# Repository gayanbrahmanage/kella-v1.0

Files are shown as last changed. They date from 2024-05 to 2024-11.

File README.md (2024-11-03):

# kella-v1.0
 Humonoid Robot Development Project

 ### Base Design and Development
 <div style="display: flex;">
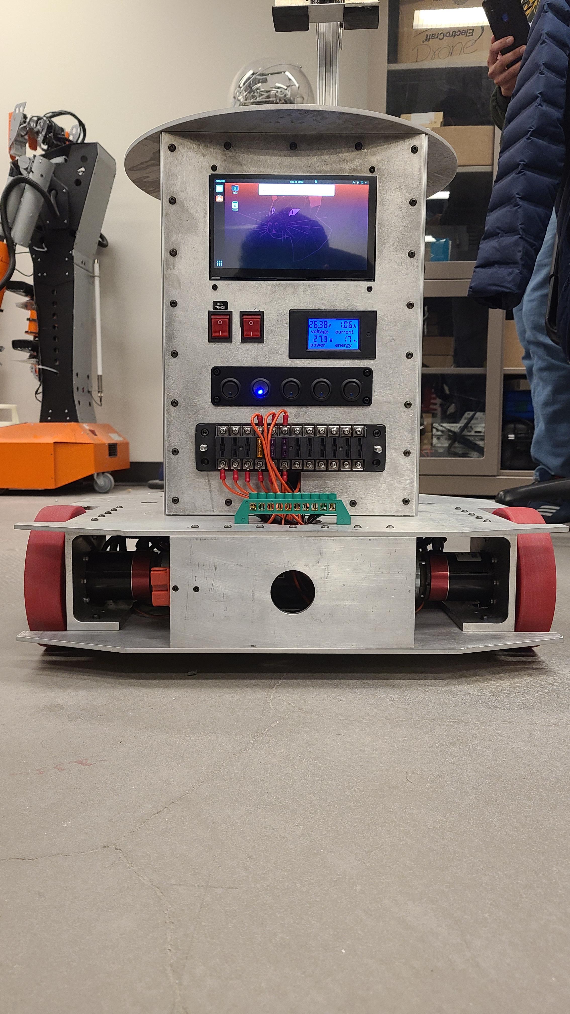
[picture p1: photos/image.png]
Example Image
 
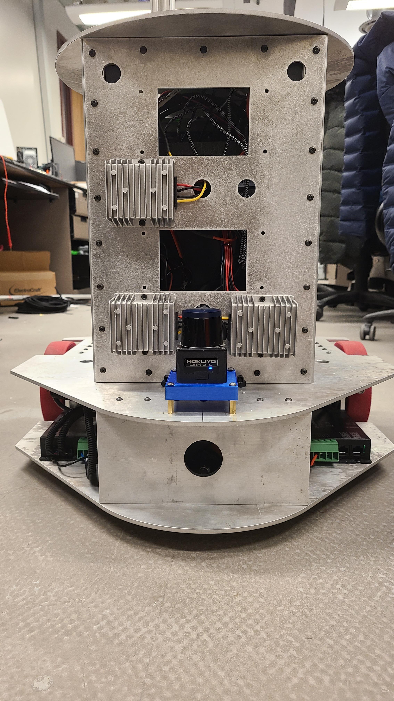
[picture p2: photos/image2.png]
Example Image
 
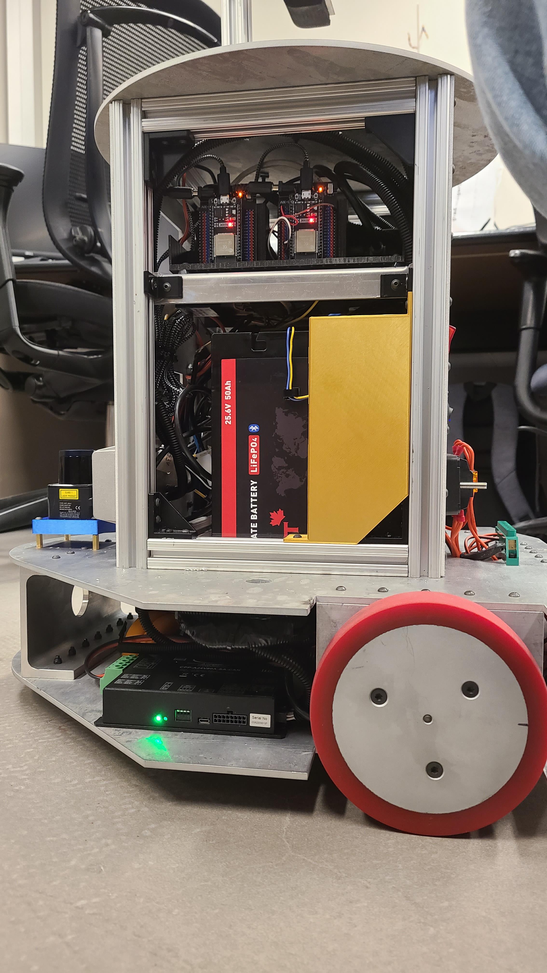
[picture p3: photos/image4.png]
Example Image
 
 </div>
 
 ### YouTube Video-Base Manual Mode Testing

My YouTube Video (https://www.youtube.com/watch?v=laG0K3bYE8s)

[Watch on YouTube](https://www.youtube.com/watch?v=laG0K3bYE8s)

My YouTube Video (https://www.youtube.com/watch?v=bEIRYtwlFlk)

# Design Power Point 

[View Design PPT](photos/pdf.pdf)

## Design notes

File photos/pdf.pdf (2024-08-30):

# Receptionist Robot

### Design and Development of A Humanoid Robot

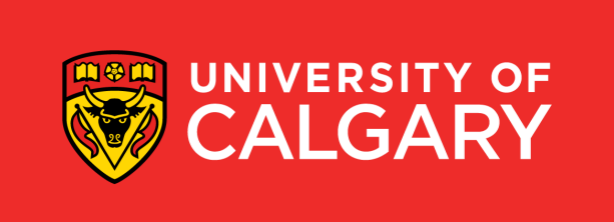
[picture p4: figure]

### 25 January 2022

2

# Modules (Electrical/Electronics)

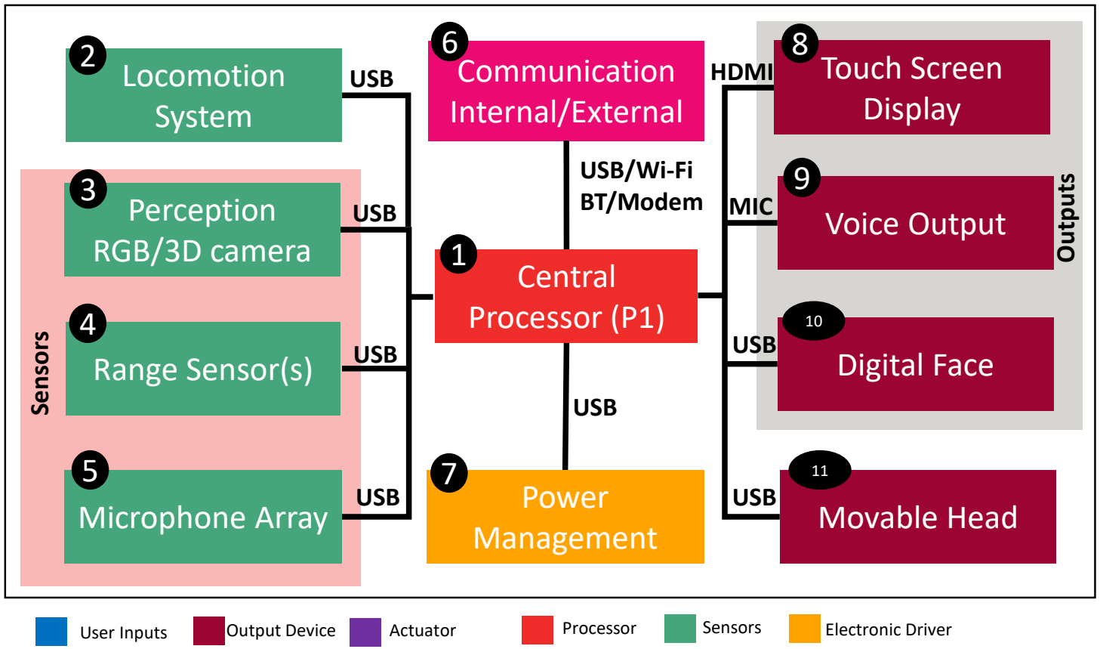
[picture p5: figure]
Locomotion System; Perception RGB/3D camera; Range Sensor(s); Microphone Array; Power; Management; Central Processor (P1); Communication Internal/External; Touch Screen Display; Voice Output; Digital Face; Movable Head USB; USB; HDMI; MIC; USB/Wi-Fi BT/Modem; Sensors; User Inputs; Output Device; Actuator; Processor; Electronic Driver; Outputs

- Central Processor P(1)-Running
master node (node handler). All nodes are registered under this node.
- Locomotion Node runs on an independent processor (P2) connected to P1.
- All the sensors are connected to Processor 3 (P3) and connected P1.
- Output devices are connected to P1.

3

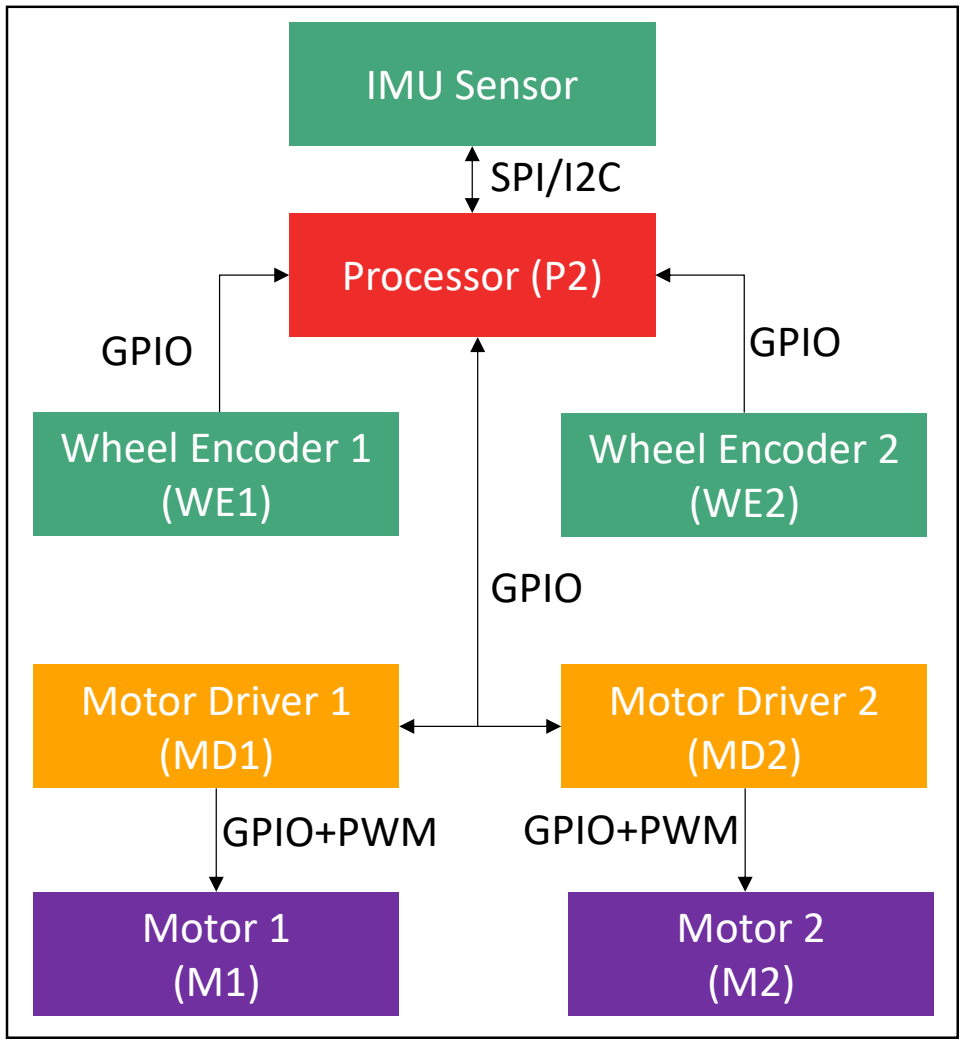
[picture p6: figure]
Wheel Encoder 2 (WE2); Wheel Encoder 1 (WE1); Motor Driver 1 (MD1); Motor 1 (M1); Motor Driver 2 (MD2); Motor 2 (M2); IMU Sensor; Processor (P2); SPI/I2C; GPIO; GPIO+PWM

# Locomotion System

- Motion control software node (stability and motion control) runs on P2 independent of the central processor.
- Receive navigation commands from P1.
- Two-wheel drive system with self balancing.
- Inputs- IMU data (SPI/I2C data Bus), Wheel Encoder data (GPIO).
- 3 Axes IMU- Orientation sensor fused with WE data.
- Motor driver- 12V direction and speed control.
- M1/M2- DC 12V motor. Attached optical quadratic wheel encoders.

4

# Perception/Sensors

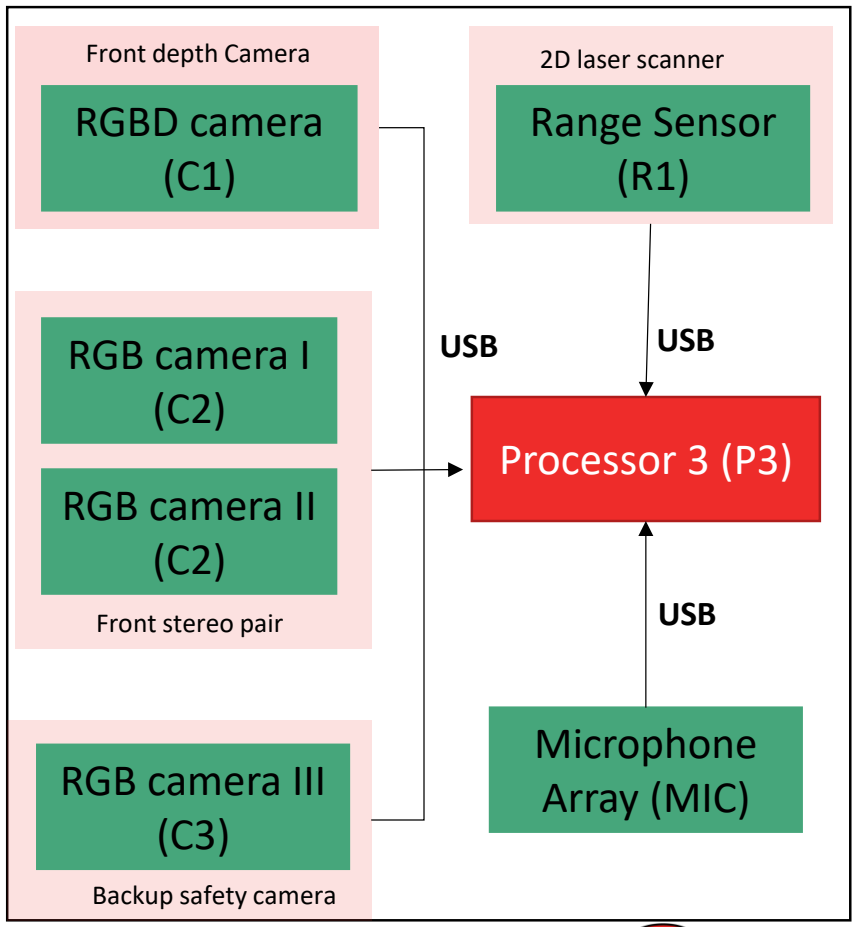
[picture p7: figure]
RGBD camera (C1); RGB camera I (C2); RGB camera II (C2); RGB camera III (C3); Range Sensor (R1); Microphone Array (MIC); Processor 3 (P3); Front depth Camera; 2D laser scanner; Front stereo pair; Backup safety camera; USB

- Front facing fixed RGB-D camera is used to capture depth data for 3D object detection and tracking up to 6m range.
- C1 and C2 RGB stereo pair is mounted on the head ( eyes) to scan nearby area. The head with the stereo camera system can rotate around x and y axes.
- C3 is the fixed safety camera mounted at the back.
- R1 is used to get long-range range data up to 30m for 2D mapping that assist to path planning.
- MIC audio input for voice recognition.

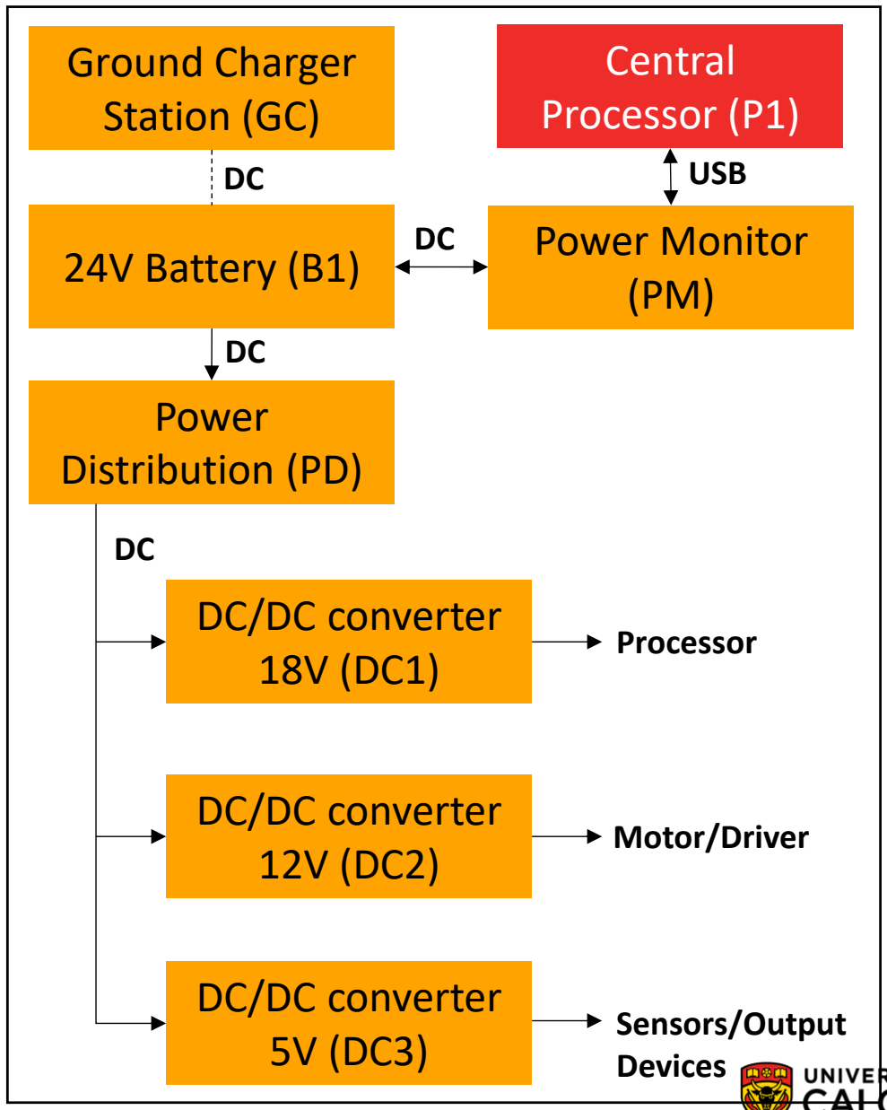
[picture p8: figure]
24V Battery (B1); Ground Charger Station (GC); Power Distribution (PD); DC/DC converter 18V (DC1); DC/DC converter 12V (DC2); DC/DC converter 5V (DC3); Power Monitor (PM); Central Processor (P1); USB; Processor; Motor/Driver; Sensors/Output Devices

5

# Power Management

- Robot is powered by rechargeable Li-Iron 24V battery pack.
- Robot can automatically docked to the charging station when charging command is received from P1.
- Power monitor continuously monitor the battery level and send data to P1.
- A power distribution board is used to distribute power to DC-to-DC converters.

6

# Movable Head/Output Devices

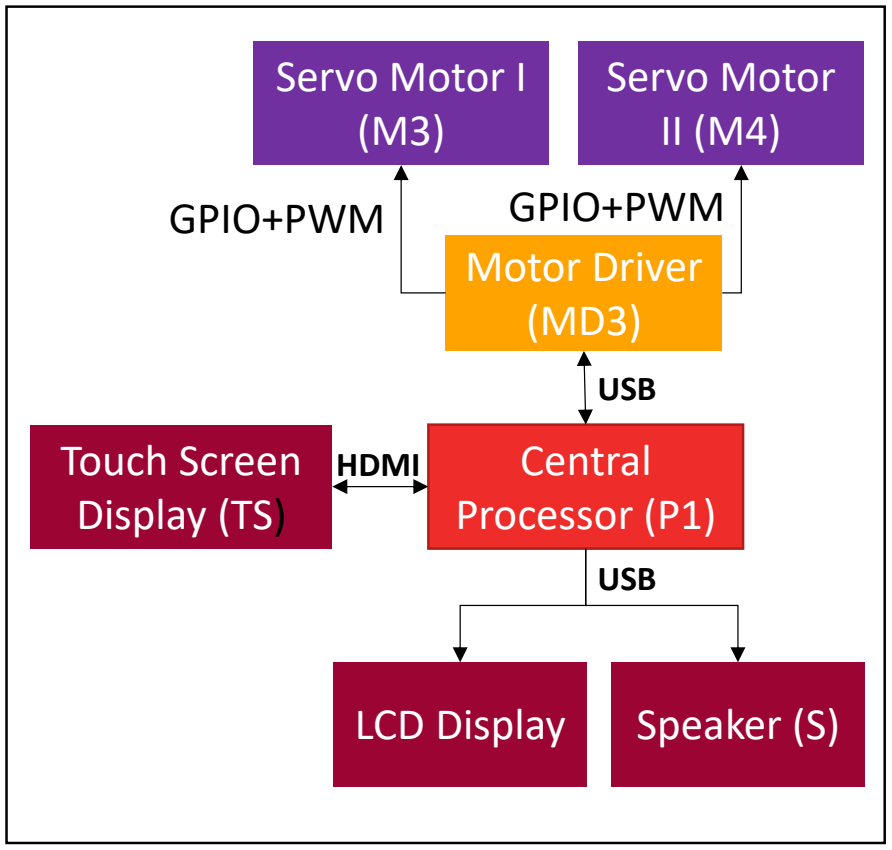
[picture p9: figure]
Servo Motor I (M3); Servo Motor II (M4); Motor Driver (MD3); LCD Display; Speaker (S); Central Processor (P1); Touch Screen Display (TS); HDMI; USB; GPIO+PWM

- Head has 2-DoF motion (rotate around x and y axes) powered by servo motors.
- Front has an LCD display to express emotions.
- A touch screen display (android device) is used provide information to users and get inputs from users.
- Speakers used to deliver voice outputs.

7

# Hardware Specifications

# | Hardware | Power | Comm | Remarks

P1 | Central Processor | 12-19V | USB, Ethernet, Wi-Fi, BT
P2 | Processor 2 | 12-19V | USB, Wi-Fi, GPIO
P3 | Processor 3 | 12-19V | USB, Wi-Fi, GPIO
M1,M2 | DC Motors | 24V
MD1, MD2 | DC Motor Drivers | 12V, 20A | USB
IMU | IMU Sensor | 5V | USB
C1 | RGBD camera | 5V | USB
C2,C3,C4 | RGB camera(s) | 5V | USB
R1 | Range Sensor | 5V | USB
MIC | Microphone Array | 5V | USB
B1 | Battery | 24V, 50C

8

# Hardware Specifications …

# | Hardware | Power | Comm | Remarks

DC1 | DC/DC converter 18V | 18V, 10A
DC2 | DC/DC converter 12V | 12V, 100A
DC3 | DC/DC converter 5V | 5V, 10A
PM | Power Monitor | 24V | USB
M3, M4 | Servo Motors | 5V, 5A | PWM, GPIO
MD3 | Motor Driver | 5V, 10A | USB
TS | Touch Screen | 5V | HDMI
LCD | LCD Display | 5V | USB
S | Speaker | 5V | AUX
GC | Ground Charger | 24V, 10A | DC
PD | Power Distribution Board | 24V, 18V, 12V,5V 100A

9

# Software Tools

- Software is developed on Robot Operating System (ROS).
- Runs on Ubuntu 18.04 LTS, C++, C-Make.
- ROS synchronous multi-threading method is used for real time operations.

### - All nodes are running independently, however they are synchronized to

maintain proper data flow.

### - Third Party Libraries:

- OpenCV-Computer Vision Library
- OpenGL- Computer Graphics Library
- Point Cloud Library
- TensorFlow- Deep learning toolkit
- Android Studio

# Software Modules

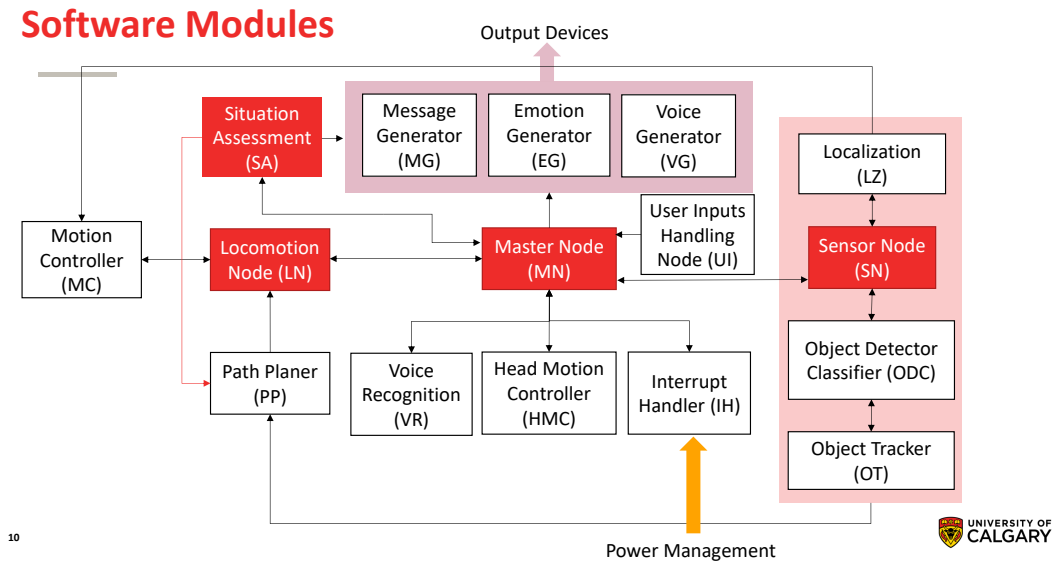
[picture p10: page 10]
Master Node (MN); Motion Controller (MC); Object Detector; Path Planer; Classifier (ODC); Interrupt Handler (IH); Voice Recognition (VR); Localization (LZ); Emotion Generator (EG); Voice Generator (VG); Message Generator (MG); Head Motion Controller (HMC); Locomotion Node (LN); Sensor Node (SN); Object Tracker (OT); Output Devices; Power Management; Situation Assessment (SA); User Inputs Handling Node (UI)

11

# Master Node

- Master ROS node runs on the central processor (P1) at 30Hz.
- Connected to all the nodes directly or through intermediate nodes.

### - Master node maintains and synchronizes dataflow from sensor input to output

commands.

12

# Motion Controller

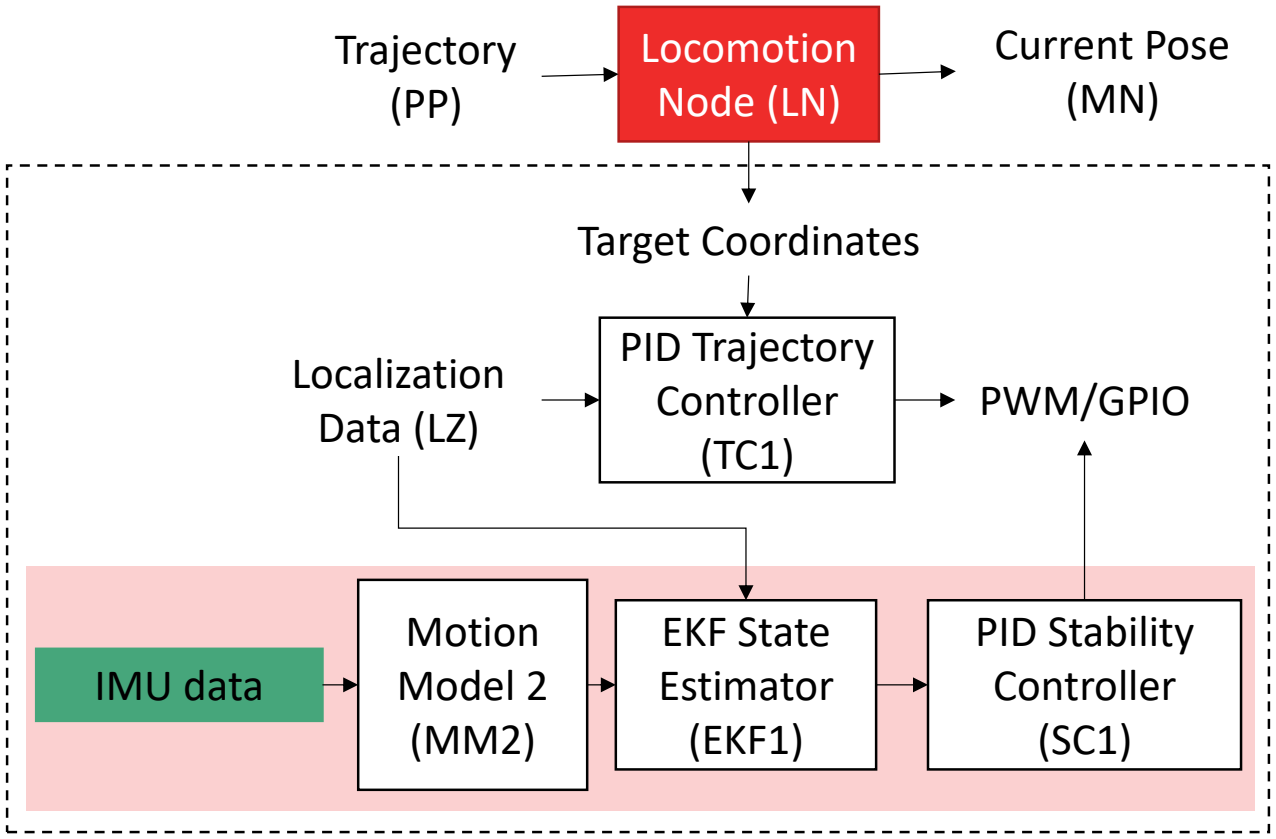
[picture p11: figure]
Target Coordinates; Locomotion Node (LN); Trajectory (PP); Current Pose (MN); PID Trajectory Controller (TC1); IMU data; EKF State Estimator (EKF1); Localization Data (LZ); PID Stability Controller (SC1); Motion Model 2 (MM2); PWM/GPIO

- Locomotion node receives trajectory information from path planner.
- Send current pose info (position and orientation) to the MN.
- LN sends discretized target coordinates to trajectory controller.
- MM1-2D robot motion model.
- MM2-Two-wheel balancing model.
- EKF1 fuse localization and IMU data to estimate current orientation.

13

# Path Planner

- Path planner compute a sequence of coordinate points from current pose the target pose.
- Obstacle's locations and their occupancy in space are taken to plan the path.
- Path must be frequently updated based on obstacles motion in the space to avoid them.
- Target point is received from the situation assessment module (SA) based on most recent and relevant input data.

Path Planner
(PP)

Localization
Data (LZ)

Target (SA)

Objects in 3D
Space (OT)

Trajectory
(PP)

14

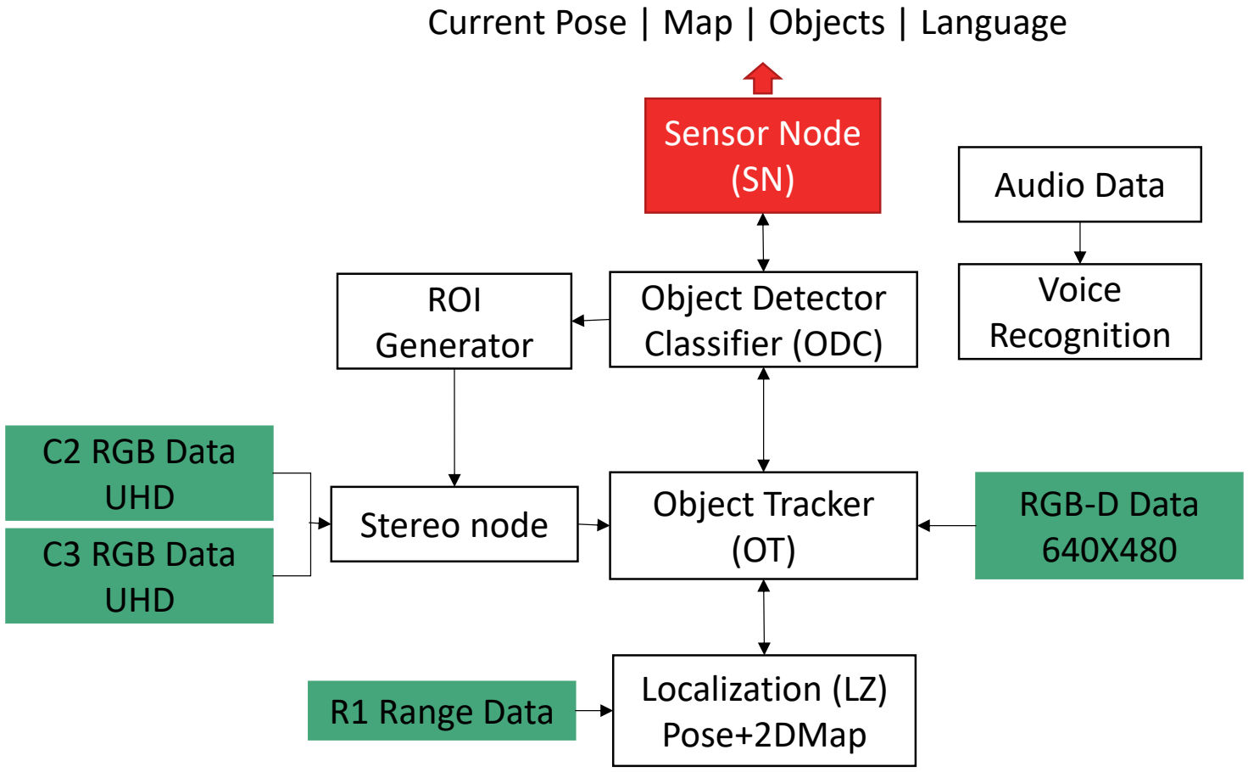
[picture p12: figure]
Sensor Node (SN); RGB-D Data 640X480; C2 RGB Data UHD C3 RGB Data UHD; R1 Range Data; Object Detector Classifier (ODC); Object Tracker (OT) Stereo node; ROI Generator; Localization (LZ) Pose+2DMap; Audio Data; Voice Recognition; Current Pose | Map | Objects | Language

# Sensor Node

- Sensor node outputs:
- Current robot pose and 2D map.
- Detected objects with
classification class ID.
- Object's location in the map.
- Language interpretation of processed audio data.
- Contains data reading programs (Sensor nodes).
- Data synchronized to closes time stamp.
- Stereo node generate 3D data based on region of interest (ROI) to reduce computation overhead.

15

# Other Nodes

Node Name | Algorithm/Method
Message Generator (MG) | To be determined

Emotion Generator (EG)

Voice Generator (VG)

Voice Recognition (VR)
Head Motion Controller (HMC)

Interrupt Handler (IH)
User Inputs Handling Node (UI)

16

# Node Specifications

Node # | Node Name | Parent Node | CPU | Speed (Min) | Inputs | Outputs | Remarks
1 | Locomotion (LN) | Master Node (MN) | P2 | 10Hz
2 | Motion Controller (MC) | Locomotion (LN) | P2 | 10Hz
3 | Path Planer (PP) | Locomotion (LN) | P2 | 10Hz
4 | Sensor Node (SN) | Master Node (MN) | P3 | 10Hz
5 | Localization (LZ) | Sensor Node (SN) | P3 | 10Hz
6 | Object Detector Classifier (ODC) | Sensor Node (SN) | P3 | 10Hz
7 | Object Tracker (OT) | Sensor Node (SN) | P3 | 10Hz
8 | Voice Recognition (VR) | Master Node (MN | P1 | 10Hz
9 | Head Motion Controller (HMC) | Master Node (MN) | P1 | 10Hz
10 | Interrupt Handler (IH) | Master Node (MN) | P1 | 30Hz
11 | Message Generator (MG) | Master Node (MN) | P1 | 10Hz
12 | Emotion Generator (EG) | Master Node (MN) | P1 | 10Hz
13 | Voice Generator (VG) | Master Node (MN) | P1 | 10Hz
14 | User Inputs Handling Node (UI) | Master Node (MN) | P1 | 10Hz

# Base Development

# Base- Mechanical Design, Fabrication and Assembling

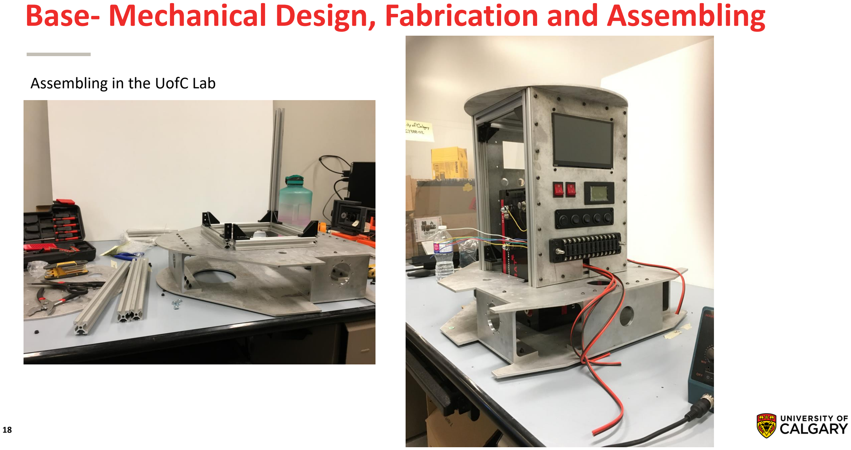
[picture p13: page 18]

18

Assembling in the UofC Lab

# Completed Base

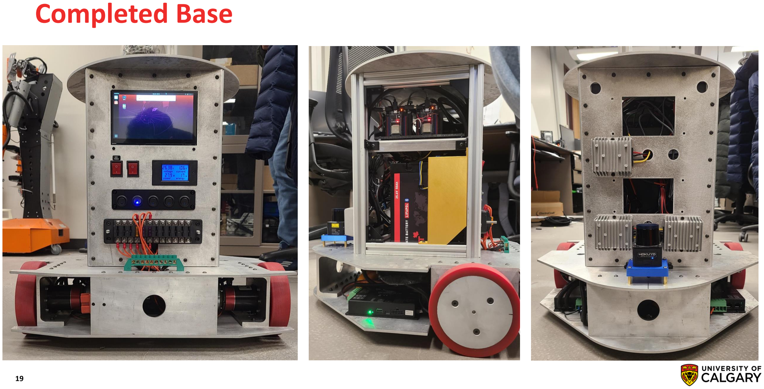
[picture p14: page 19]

19

# Completed Electronics

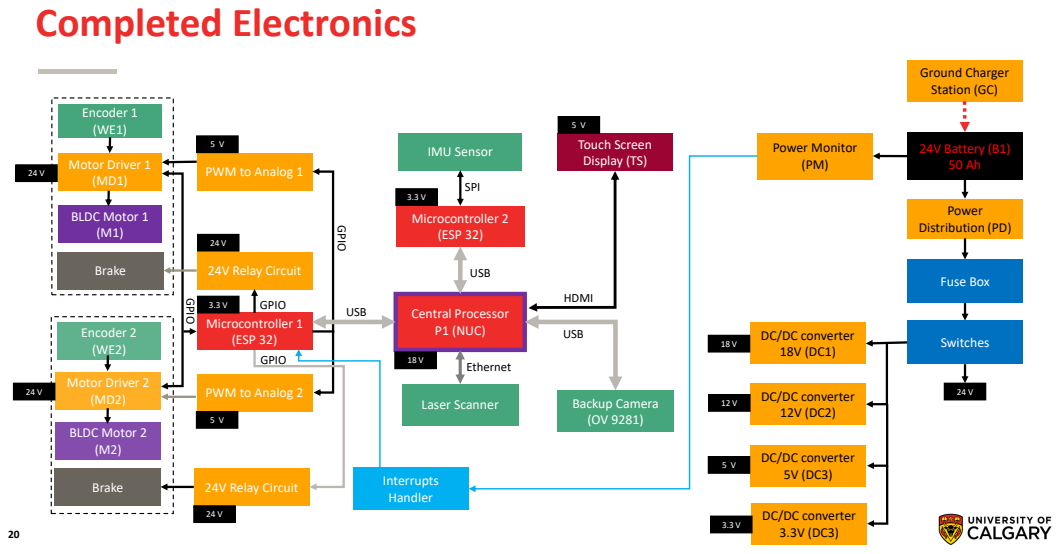
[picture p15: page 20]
Encoder 2 (WE2); Encoder 1 (WE1); Motor Driver 1 (MD1); BLDC Motor 1 (M1); Motor Driver 2 (MD2); BLDC Motor 2 (M2); IMU Sensor; Central Processor P1 (NUC); SPI; GPIO Microcontroller 1 (ESP 32); Microcontroller 2 (ESP 32); Laser Scanner; 24V Relay Circuit; Fuse Box; 24V Battery (B1) 50 Ah; Ground Charger Station (GC); Power Distribution (PD); Power Monitor (PM); Switches; Brake; Touch Screen Display (TS); Backup Camera (OV 9281); USB; GPIO; Ethernet; HDMI; Interrupts Handler

PWM to Analog 1

DC/DC converter

PWM to Analog 2

21

# Motion Controller

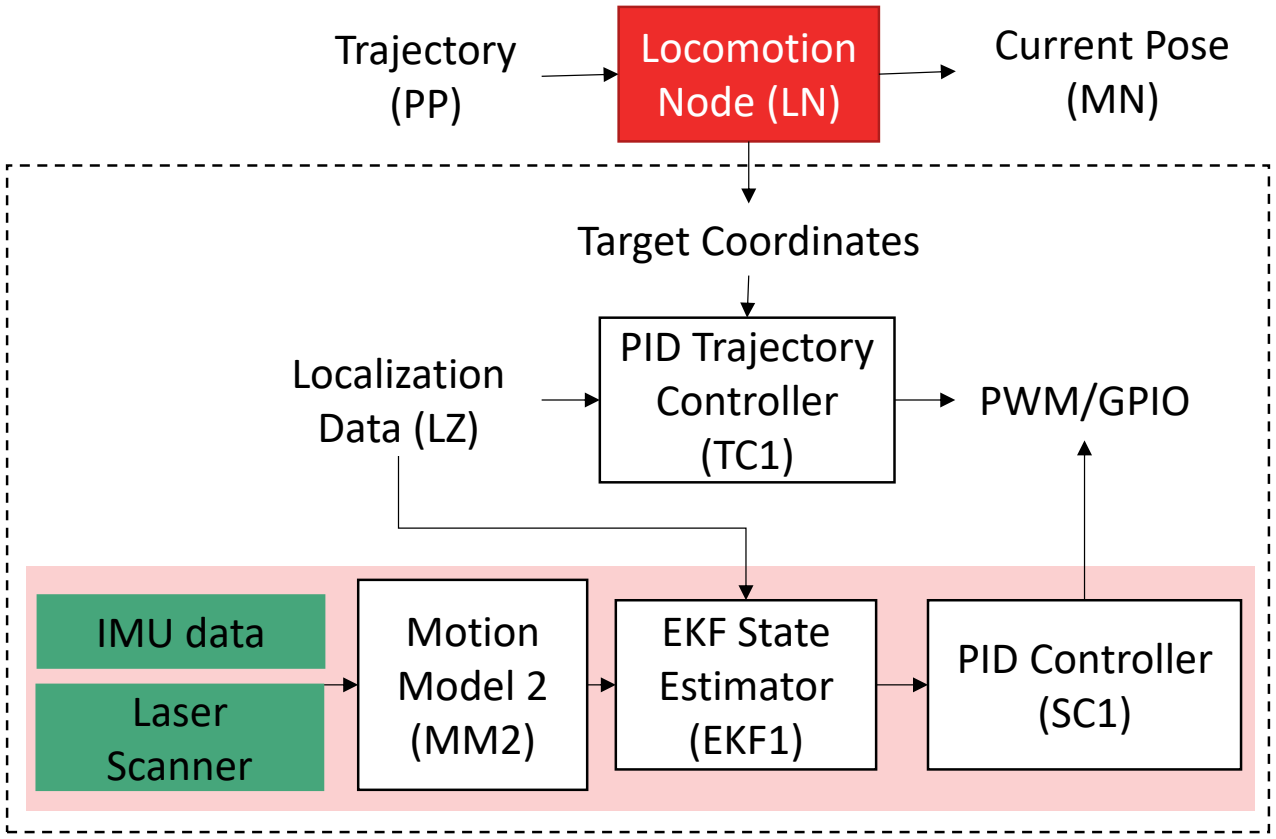
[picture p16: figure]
Target Coordinates; Locomotion Node (LN); Trajectory (PP); Current Pose (MN); PID Trajectory Controller (TC1); IMU data; EKF State; Estimator (EKF1); Localization Data (LZ); PID Controller (SC1); Motion Model 2 (MM2); PWM/GPIO; Laser Scanner

- Locomotion node receives trajectory information from path planner.
- Send current pose info (position and orientation) to the MN.
- LN sends discretized target coordinates to trajectory controller.
- MM1-2D robot motion model.
- MM2-Two-wheel balancing model.
- EKF1 fuse localization and IMU data to estimate current orientation.

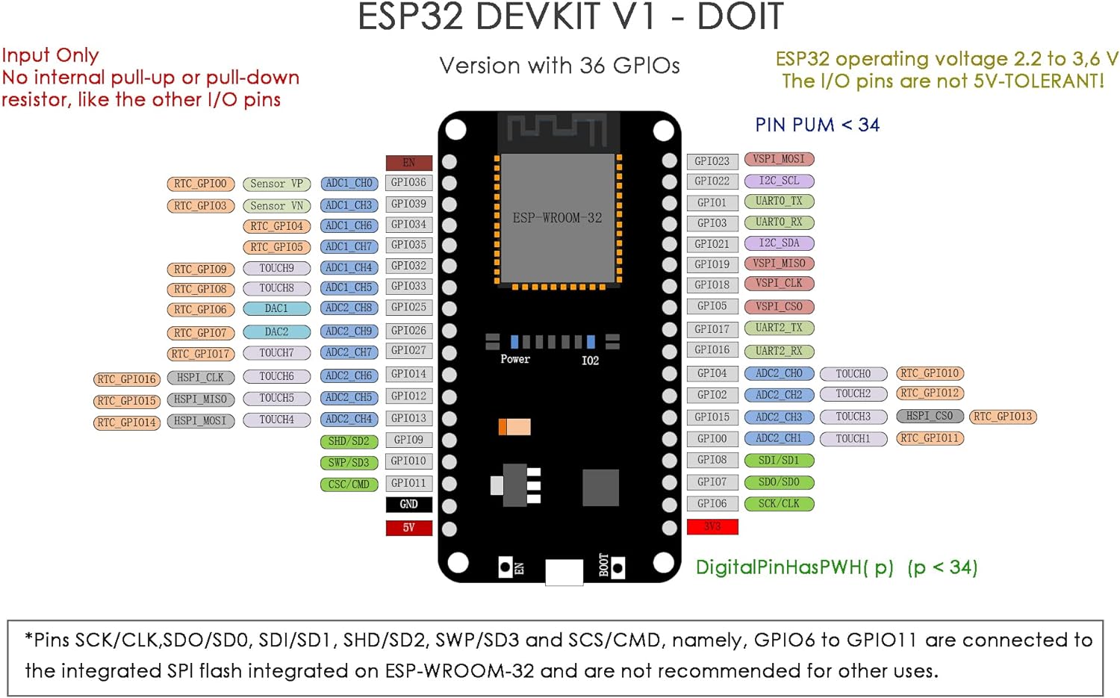
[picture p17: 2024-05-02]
ESP32_CODE/Pinout.jpg

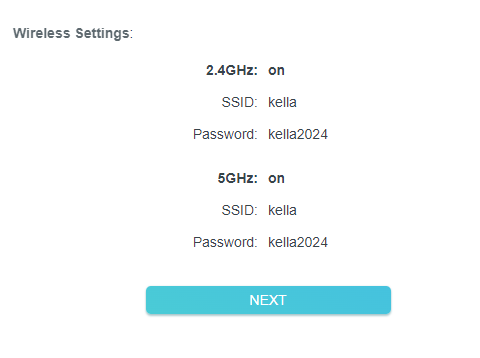
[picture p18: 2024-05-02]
Wireless.PNG

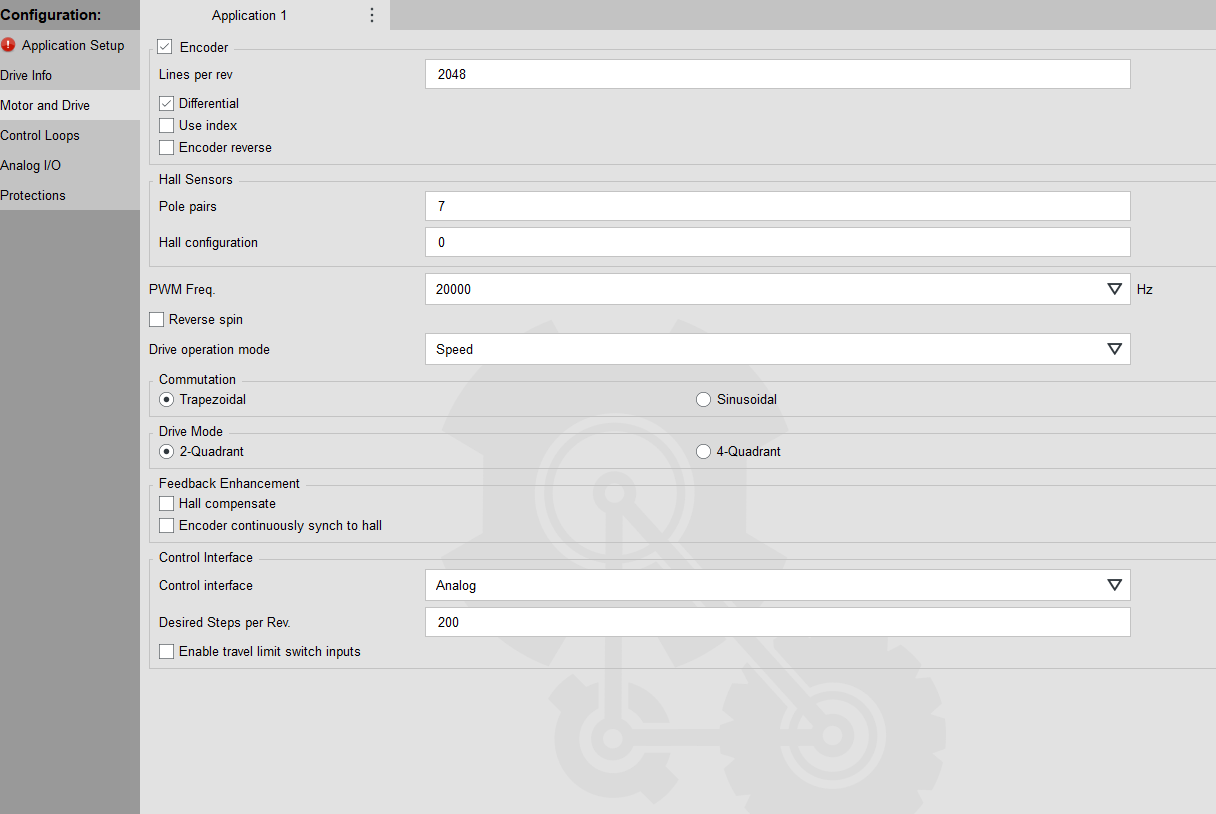
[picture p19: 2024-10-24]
MotorDriver/MPW52/MotorDrive.PNG

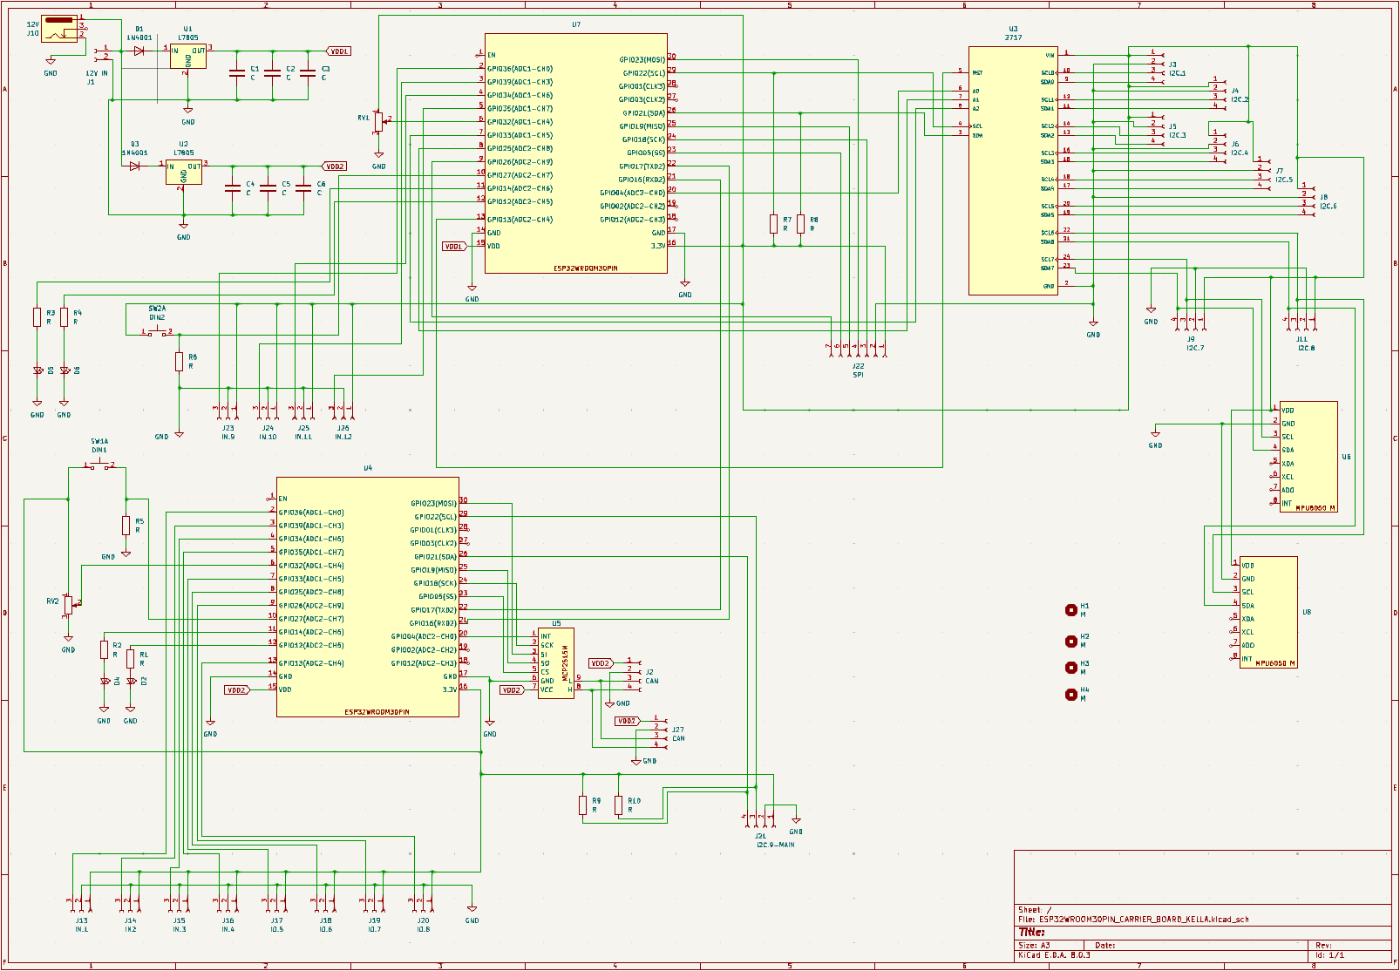
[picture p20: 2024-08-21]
KELLAPCB/ESP32KiCAD/Circuit.PNG

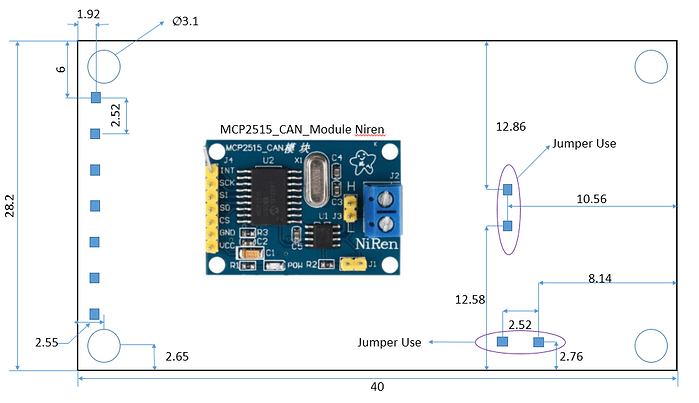
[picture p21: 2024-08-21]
KELLAPCB/ESP32KiCAD/MCP2515.png

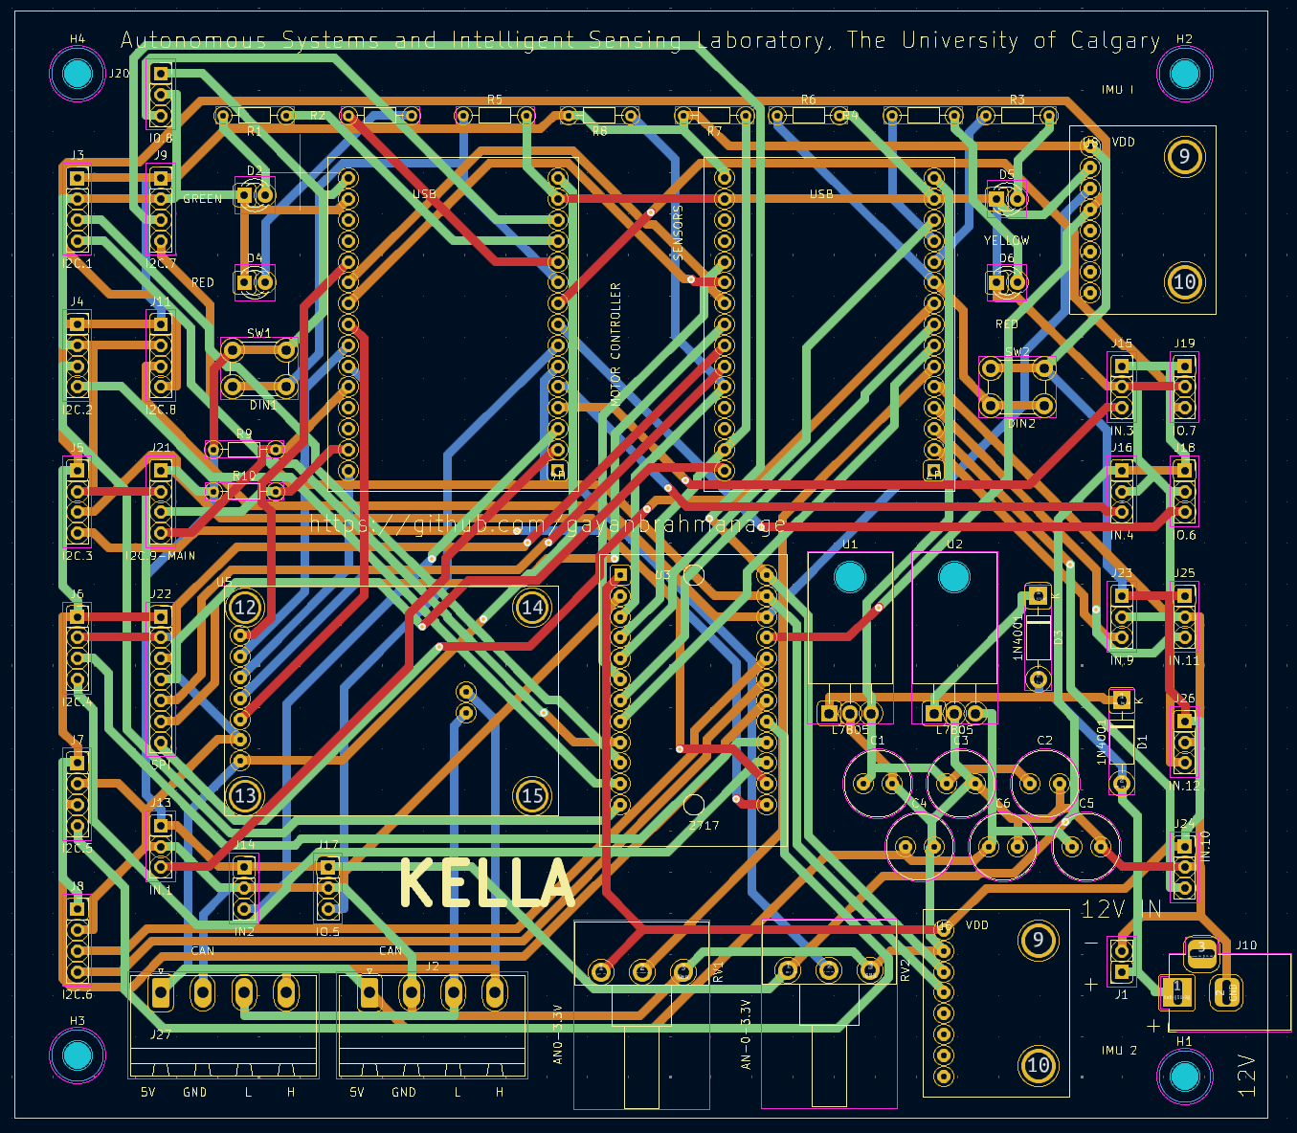
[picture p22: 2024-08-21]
KELLAPCB/ESP32KiCAD/PCB.PNG

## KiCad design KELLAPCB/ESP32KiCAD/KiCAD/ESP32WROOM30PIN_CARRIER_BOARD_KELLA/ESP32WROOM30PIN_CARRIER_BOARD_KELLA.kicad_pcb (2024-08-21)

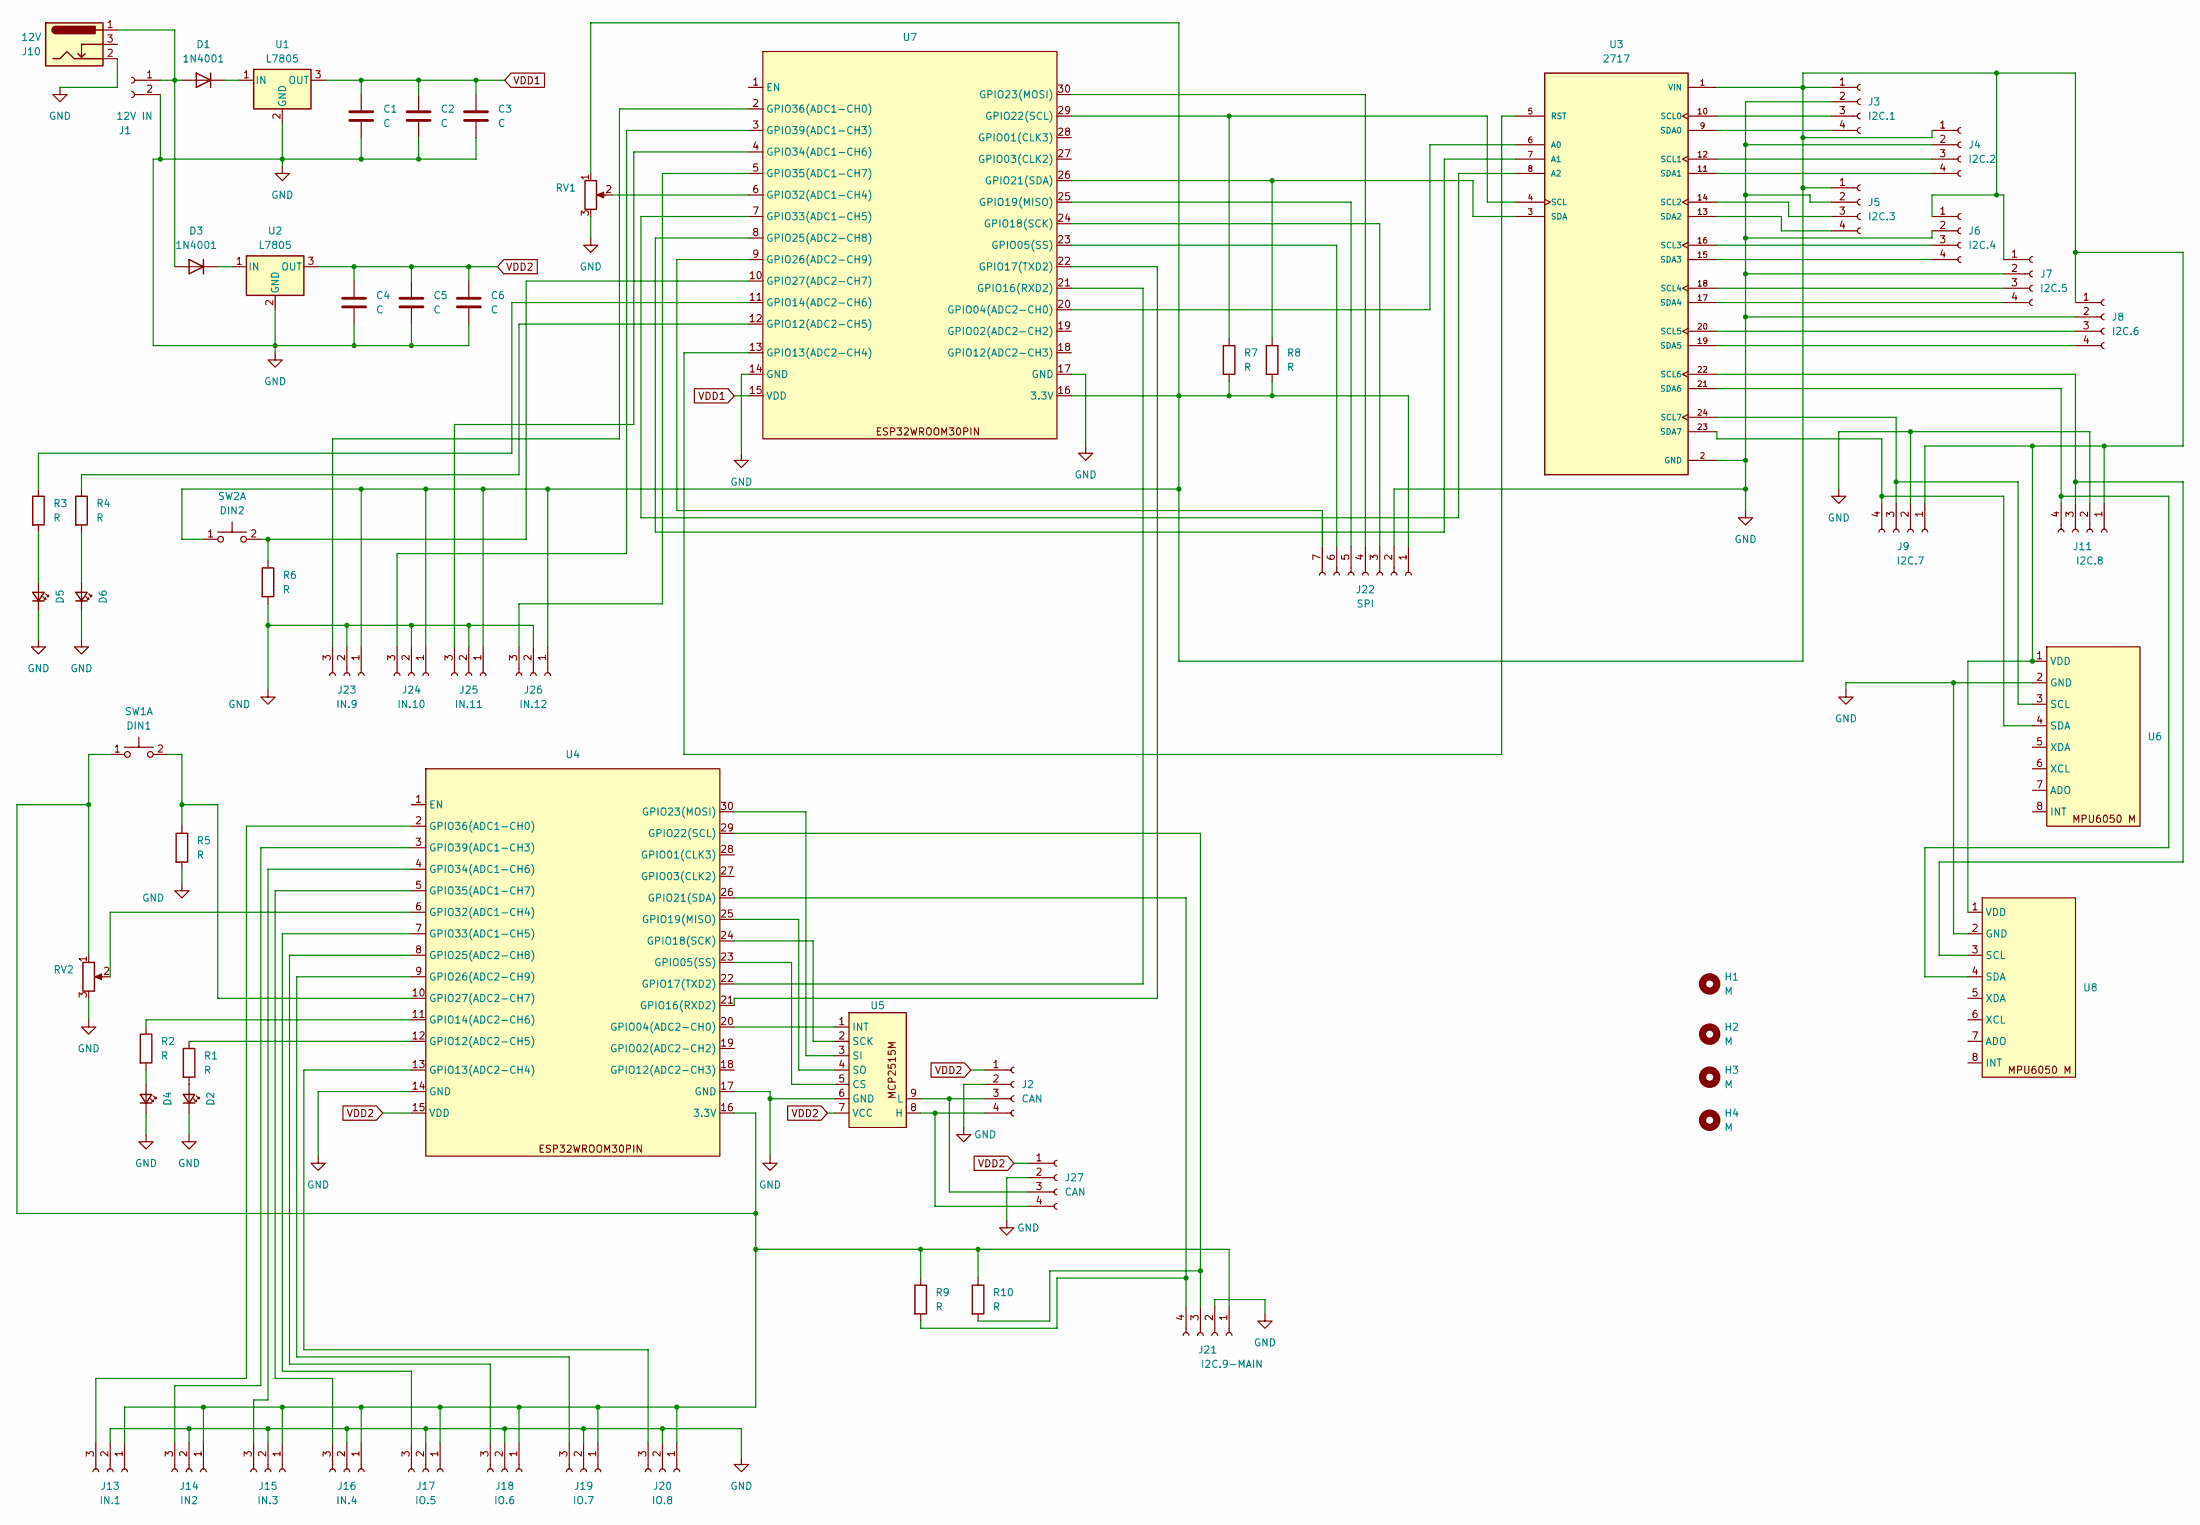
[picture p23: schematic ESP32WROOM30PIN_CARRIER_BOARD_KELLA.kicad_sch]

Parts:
C1, C2, C3, C4, C5, C6: C; C_Radial_D8.0mm_H7.0mm_P3.50mm
D1, D3: 1N4001; D_DO-41_SOD81_P10.16mm_Horizontal
D2: GREEN; LED_D3.0mm_IRGrey
D4, D6: RED; LED_D3.0mm_IRGrey
D5: YELLOW; LED_D3.0mm_IRGrey
H1, H2, H3, H4: M; MountingHole_3.2mm_M3
J1: 12V IN; PinSocket_1x02_P2.54mm_Vertical
J2, J27: CAN; PhoenixContact_MSTBA_2,5_4-G-5,08_1x04_P5.08mm_Horizontal
J3: I2C.1; PinSocket_1x04_P2.54mm_Vertical
J4: I2C.2; PinSocket_1x04_P2.54mm_Vertical
J5: I2C.3; PinSocket_1x04_P2.54mm_Vertical
J6: I2C.4; PinSocket_1x04_P2.54mm_Vertical
J7: I2C.5; PinSocket_1x04_P2.54mm_Vertical
J8: I2C.6; PinSocket_1x04_P2.54mm_Vertical
J9: I2C.7; PinSocket_1x04_P2.54mm_Vertical
J10: 12V; BarrelJack_Horizontal
J11: I2C.8; PinSocket_1x04_P2.54mm_Vertical
J13: IN.1; PinSocket_1x03_P2.54mm_Vertical
J14: IN2; PinSocket_1x03_P2.54mm_Vertical
J15: IN.3; PinSocket_1x03_P2.54mm_Vertical
J16: IN.4; PinSocket_1x03_P2.54mm_Vertical
J17: IO.5; PinSocket_1x03_P2.54mm_Vertical
J18: IO.6; PinSocket_1x03_P2.54mm_Vertical
J19: IO.7; PinSocket_1x03_P2.54mm_Vertical
J20: IO.8; PinSocket_1x03_P2.54mm_Vertical
J21: I2C.9-MAIN; PinSocket_1x04_P2.54mm_Vertical
J22: SPI; PinSocket_1x07_P2.54mm_Vertical
J23: IN.9; PinSocket_1x03_P2.54mm_Vertical
J24: IN.10; PinSocket_1x03_P2.54mm_Vertical
J25: IN.11; PinSocket_1x03_P2.54mm_Vertical
J26: IN.12; PinSocket_1x03_P2.54mm_Vertical
R1, R2, R3, R4, R5, R6, R7, R8, R9, R10: R; R_Axial_DIN0204_L3.6mm_D1.6mm_P7.62mm_Horizontal
RV1: AN0-3.3V; Potentiometer_Piher_T-16H_Single_Horizontal
RV2: AN-0-3.3V; Potentiometer_Piher_T-16H_Single_Horizontal
SW1: DIN1; SW_PUSH_6mm_H4.3mm
SW2: DIN2; SW_PUSH_6mm_H4.3mm
U1, U2: L7805; TO-220-3_Horizontal_TabDown
U3: 2717; Module2717_TCA9548A; PARTREV Sep 11, 2015
U4, U7: ESP32WROOM30PIN
U5: MCP2515Mf
U6, U8: MPU6050M

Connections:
GND: C1.2, C2.2, C3.2, C4.2, C5.2, C6.2, D2.1 (K), D4.1 (K), D5.1 (K), D6.1 (K), J1.2, J2.2, J3.2, J4.2, J5.2, J6.2, J7.2, J8.2, J9.2, J10.2, J11.2, J13.2, J14.2, J15.2, J16.2, J17.2, J18.2, J19.2, J20.2, J21.2, J22.2, J23.2, J24.2, J25.2, J26.2, J27.2, R5.2, R6.2, RV1.3, RV2.3, U1.2 (GND), U2.2 (GND), U3.2 (GND), U4.14 (GND), U4.17 (GND), U5.6 (GND), U6.2 (GND), U7.14 (GND), U7.17 (GND), U8.2 (GND)
unnamed: D1.2 (A), D3.2 (A), J1.1, J10.1
unnamed: D1.1 (K), U1.1 (IN)
unnamed: D2.2 (A), R1.2
unnamed: D3.1 (K), U2.1 (IN)
unnamed: D4.2 (A), R2.2
unnamed: D5.2 (A), R3.2
unnamed: D6.2 (A), R4.2
unnamed: J2.3, J27.3, U5.9 (L)
unnamed: J2.4, J27.4, U5.8 (H)
unnamed: J3.3, U3.10 (SCL0)
unnamed: J3.4, U3.9 (SDA0)
unnamed: J4.3, U3.12 (SCL1)
unnamed: J4.4, U3.11 (SDA1)
unnamed: J5.3, U3.14 (SCL2)
unnamed: J5.4, U3.13 (SDA2)
unnamed: J6.3, U3.16 (SCL3)
unnamed: J6.4, U3.15 (SDA3)
unnamed: J7.3, U3.18 (SCL4)
unnamed: J7.4, U3.17 (SDA4)
unnamed: J8.3, U3.20 (SCL5)
unnamed: J8.4, U3.19 (SDA5)
unnamed: J9.3, U3.24 (SCL7), U6.3 (SCL)
unnamed: J9.4, U3.23 (SDA7), U6.4 (SDA)
unnamed: J3.1, J4.1, J5.1, J6.1, J7.1, J8.1, J9.1, J11.1, J22.1, J23.1, J24.1, J25.1, J26.1, R7.2, R8.2, RV1.1, SW2.1 (C), U3.1 (VIN), U6.1 (VDD), U7.16 (3.3V), U8.1 (VDD)
unnamed: J11.3, U3.22 (SCL6), U8.3 (SCL)
unnamed: J11.4, U3.21 (SDA6), U8.4 (SDA)
unnamed: J13.1, J14.1, J15.1, J16.1, J17.1, J18.1, J19.1, J20.1, J21.1, R9.1, R10.1, RV2.1, SW1.1 (C), U4.16 (3.3V)
unnamed: J13.3, U4.2 (GPIO36(ADC1-CH0))
unnamed: J14.3, U4.3 (GPIO39(ADC1-CH3))
unnamed: J15.3, U4.4 (GPIO34(ADC1-CH6))
unnamed: J16.3, U4.5 (GPIO35(ADC1-CH7))
unnamed: J17.3, U4.7 (GPIO33(ADC1-CH5))
unnamed: J18.3, U4.8 (GPIO25(ADC2-CH8))
unnamed: J19.3, U4.9 (GPIO26(ADC2-CH9))
unnamed: J20.3, U4.13 (GPIO13(ADC2-CH4))
unnamed: J21.3, R10.2, U4.29 (GPIO22(SCL))
unnamed: J21.4, R9.2, U4.26 (GPIO21(SDA))
unnamed: J22.3, U7.24 (GPIO18(SCK))
unnamed: J22.4, U7.30 (GPIO23(MOSI))
unnamed: J22.5, U7.25 (GPIO19(MISO))
unnamed: J22.6, U7.23 (GPIO05(SS))
unnamed: J22.7, U7.9 (GPIO26(ADC2-CH9))
unnamed: J23.3, U7.2 (GPIO36(ADC1-CH0))
unnamed: J24.3, U7.3 (GPIO39(ADC1-CH3))
unnamed: J25.3, U7.4 (GPIO34(ADC1-CH6))
unnamed: J26.3, U7.5 (GPIO35(ADC1-CH7))
unnamed: R5.1, SW1.2 (D), U4.10 (GPIO27(ADC2-CH7))
unnamed: R6.1, SW2.2 (D), U7.10 (GPIO27(ADC2-CH7))
unnamed: U3.6 (A0), U7.20 (GPIO04(ADC2-CH0))
unnamed: U3.7 (A1), U7.8 (GPIO25(ADC2-CH8))
unnamed: U3.8 (A2), U7.7 (GPIO33(ADC1-CH5))
unnamed: U3.5 (RST), U7.13 (GPIO13(ADC2-CH4))
unnamed: R7.1, U3.4 (SCL), U7.29 (GPIO22(SCL))
unnamed: R8.1, U3.3 (SDA), U7.26 (GPIO21(SDA))
unnamed: U4.20 (GPIO04(ADC2-CH0)), U5.1 (INT)
unnamed: U4.23 (GPIO05(SS)), U5.5 (CS)
unnamed: R1.1, U4.12 (GPIO12(ADC2-CH5))
unnamed: R2.1, U4.11 (GPIO14(ADC2-CH6))
unnamed: U4.21 (GPIO16(RXD2)), U7.22 (GPIO17(TXD2))
unnamed: U4.22 (GPIO17(TXD2)), U7.21 (GPIO16(RXD2))
unnamed: U4.24 (GPIO18(SCK)), U5.2 (SCK)
unnamed: U4.25 (GPIO19(MISO)), U5.4 (SO)
unnamed: U4.30 (GPIO23(MOSI)), U5.3 (SI)
unnamed: RV2.2, U4.6 (GPIO32(ADC1-CH4))
unnamed: R4.1, U7.12 (GPIO12(ADC2-CH5))
unnamed: R3.1, U7.11 (GPIO14(ADC2-CH6))
unnamed: RV1.2, U7.6 (GPIO32(ADC1-CH4))
VDD1: C1.1, C2.1, C3.1, U1.3 (OUT), U7.15 (VDD)
VDD2: C4.1, C5.1, C6.1, J2.1, J27.1, U2.3 (OUT), U4.15 (VDD), U5.7 (VCC)

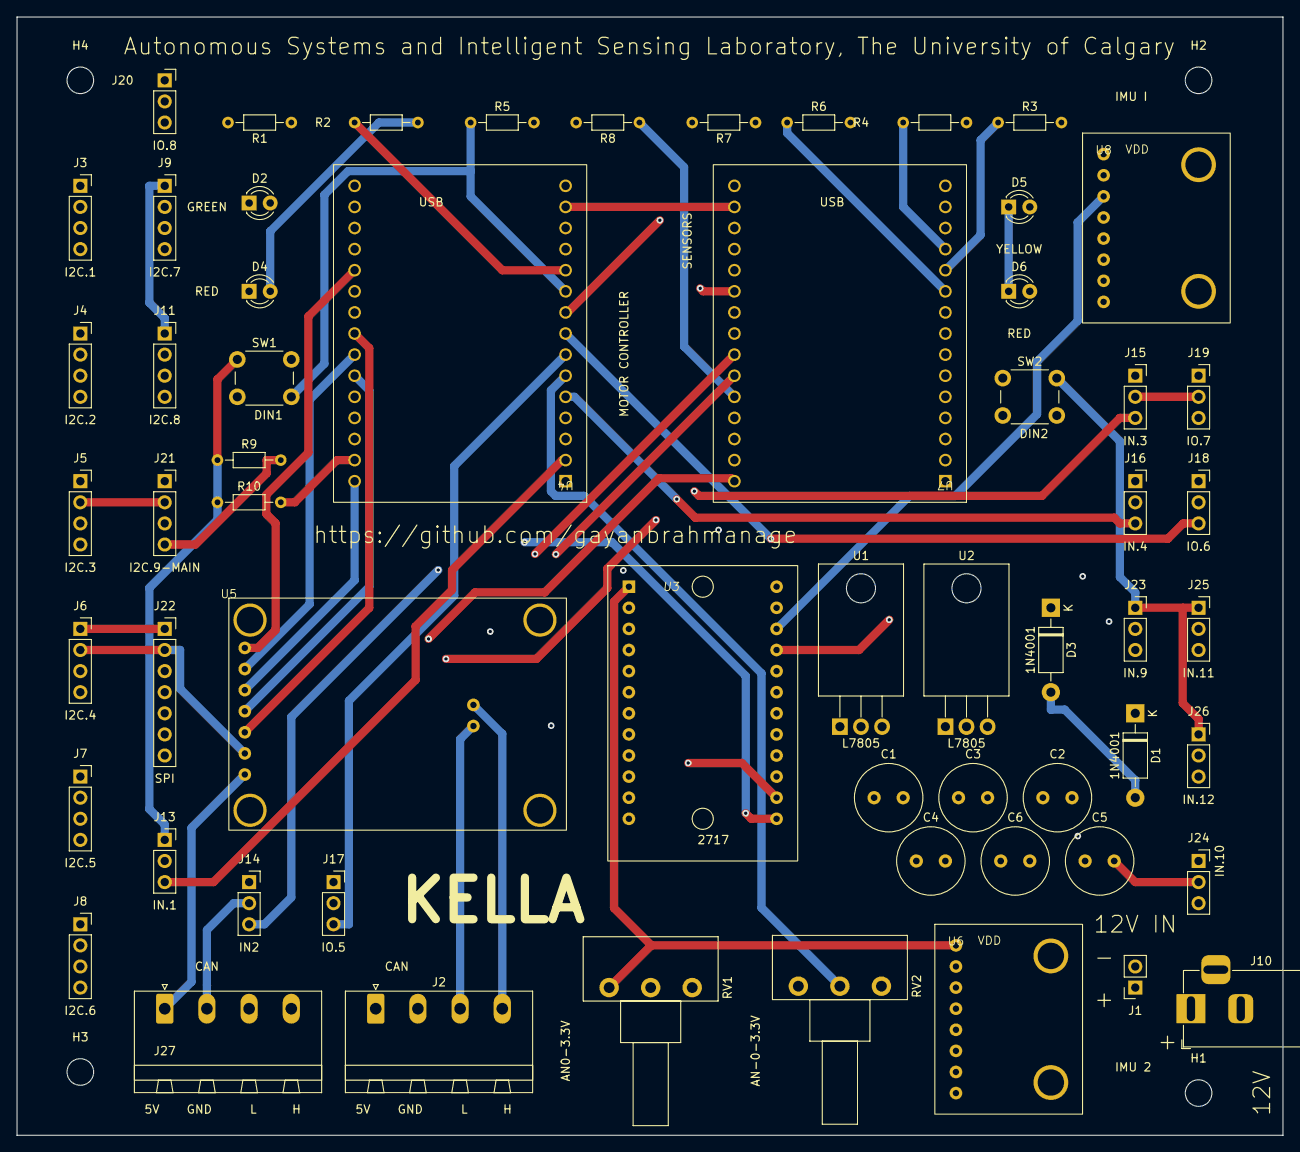
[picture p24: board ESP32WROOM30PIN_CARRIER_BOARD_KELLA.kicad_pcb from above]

Board: 4 copper layers, 152.4 x 134.6 mm, 64 parts (0 on the bottom side), 70 nets.

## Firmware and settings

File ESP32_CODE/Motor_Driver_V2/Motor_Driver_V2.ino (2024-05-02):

#include <esp_now.h>
#include <WiFi.h>
#include <Wire.h>

uint8_t broadcastAddress[] = {0xC8, 0xF0, 0x9E, 0x7B, 0x73, 0xBC}; //master driver
bool success;


typedef struct message {
    int motor1_speed=0;
    int motor2_speed=0;
    bool motor1_dir=LOW;
    bool motor2_dir=HIGH;
    bool EN1=HIGH;
    bool EN2=HIGH;
    bool Brake1=LOW;
    bool Brake2=LOW;
} message;


message send_message;
message received_message;
esp_now_peer_info_t peerInfo;

const int led_Y= 4;
const int led_B= 2;
const int led_G= 25;
const int led_R= 26;

const int freq = 100;
const int resolution = 8;

const int pwmChannel1 = 0;
const int enable1Pin1 = 16; 
const int input1 = 0; 
const int EN1=5;
const int Dir1=32;
const int Brake1=12;
const int Ready1=27;
int dutyCycle1 = 0;
bool direction1_cmd=LOW;
bool enable1_cmd=HIGH;
bool Brake1_cmd=LOW;

const int pwmChannel2 = 1;
const int enable1Pin2 = 17; 
const int input2 = 15; 
const int EN2=18;
const int Dir2=33;
const int Brake2=13;
const int Ready2=14;
int dutyCycle2 = 0;
bool direction2_cmd=HIGH;
bool enable2_cmd=HIGH;
bool Brake2_cmd=LOW;

void OnDataSent(const uint8_t *mac_addr, esp_now_send_status_t status) {
  
  if (status ==0){
    success = true;
  }
  else{
    success = false;
  }
}

void OnDataRecv(const uint8_t * mac, const uint8_t *incomingData, int len) {
  memcpy(&received_message, incomingData, sizeof(received_message));
  dutyCycle1=received_message.motor1_speed;
  dutyCycle2=received_message.motor2_speed;
  direction1_cmd=received_message.motor1_dir;
  direction2_cmd=received_message.motor2_dir;
}

void setup() {  

  WiFi.mode(WIFI_STA);
  // Init ESP-NOW
  if (esp_now_init() != ESP_OK) {
    return;
  }

  // Once ESPNow is successfully Init, we will register for Send CB to
  // get the status of Trasnmitted packet
  esp_now_register_send_cb(OnDataSent);
  
  // Register peer
  memcpy(peerInfo.peer_addr, broadcastAddress, 6);
  peerInfo.channel = 0;  
  peerInfo.encrypt = false;
  
  // Add peer        
  if (esp_now_add_peer(&peerInfo) != ESP_OK){
    return;
  }
  // Register for a callback function that will be called when data is received
  esp_now_register_recv_cb(OnDataRecv);
  
  pinMode(led_Y, OUTPUT);
  pinMode(led_B, OUTPUT);
  //pinMode(led_G, OUTPUT);
  //pinMode(led_R, OUTPUT);

  pinMode(EN1, OUTPUT);
  pinMode(EN2, OUTPUT);
  pinMode(Dir1, OUTPUT);
  pinMode(Dir2, OUTPUT);
  pinMode(Brake1, OUTPUT);
  pinMode(Brake2, OUTPUT);

  pinMode(input1, INPUT);
  pinMode(input2, INPUT);
  
  pinMode(Ready1, INPUT);
  pinMode(Ready2, INPUT);

  Serial.begin(115200);
  delay(1000);
  
  pinMode(pwmChannel1, OUTPUT);
  ledcSetup(pwmChannel1, freq, resolution);

  pinMode(pwmChannel2, OUTPUT);
  ledcSetup(pwmChannel2, freq, resolution);

  // attach the channel to the GPIO to be controlled
  ledcAttachPin(led_R, pwmChannel1);
  ledcAttachPin(enable1Pin1, pwmChannel1);

  ledcAttachPin(led_G, pwmChannel2);
  ledcAttachPin(enable1Pin2, pwmChannel2);
}

void loop() {

  esp_err_t result = esp_now_send(broadcastAddress, (uint8_t *) &send_message, sizeof(send_message));

  ledcWrite(pwmChannel1, dutyCycle1); 
  ledcWrite(pwmChannel2, dutyCycle2);  


  digitalWrite(EN1, enable1_cmd);
  digitalWrite(EN2, enable2_cmd);

  digitalWrite(Brake1, Brake1_cmd);
  digitalWrite(Brake2, Brake2_cmd);

  digitalWrite(Dir1, direction1_cmd);
  digitalWrite(Dir2, direction2_cmd);

  if(!digitalRead(Ready1)){
    digitalWrite(led_B, HIGH);
  }else{
    digitalWrite(led_B, LOW);
  }

  if(!digitalRead(Ready2)){
    digitalWrite(led_Y, HIGH);
  }else{
    digitalWrite(led_Y, LOW);
  }

}

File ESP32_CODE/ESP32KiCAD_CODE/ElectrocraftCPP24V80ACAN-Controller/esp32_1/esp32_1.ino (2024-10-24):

#include <SPI.h>
#include <mcp2515.h>
#include "message.h"
#include "io.h"
#include "RF_remote.h"

// Initialize MCP2515
MCP2515 mcp2515(5);

byte CPP1=0x01;
MotorData Motor1Data;

byte CPP2=0x02;
MotorData Motor2Data;

RF remote=RF();

void setup() {
  
  init_io();

  digitalWrite(IO5Pin, HIGH); // MPW52 CAN enable external input

  configureCAN();
  delay(10);
  Reset(CPP1);
  delay(10);
  Reset(CPP2);
  delay(10);
  enable(CPP1,Motor1Data);
  delay(10);
  enable(CPP2,Motor2Data);
  delay(10);

  //remote
  remote.init();
  
}

void loop() {

  remote.get_remote_input(Motor1Data, Motor2Data);
  
  GET_Drive_Status(CPP1, Motor1Data);
  GET_Drive_Status(CPP2, Motor2Data);

  output(Motor2Data);
  
//  Serial.println(Motor2Data.get_ready);
//  Serial.println(Motor2Data.get_enable);
//  Serial.println(Motor2Data.get_fault);

  buttonState = digitalRead(buttonPin);
  potValue = analogRead(potPin);

  //Motor1Data.set_Move_Relative=potValue-2048;
  //Motor2Data.set_Move_Relative=potValue-2048;
  
  
  if (buttonState == HIGH) {
     Reset(CPP1);
     delay(1000);
     SET_Digital_Output( CPP1);
     delay(1000);
     enable(CPP1,Motor1Data);
     delay(1000);

     Reset(CPP2);
     delay(1000);
     enable(CPP2,Motor2Data);
     delay(1000);
     
//     move_speed(CPP1);
//     delay(1000);
//     move_current(CPP1);
//     delay(1000);
//     brake(CPP1, 0x00);
     
  }else{

  }
  
  if(Motor1Data.get_enable & Motor1Data.get_ready){
    move_relative(CPP1,Motor1Data); 
    //Motor1Data.set_Move_speed =Motor1Data.set_Move_Relative;
    //move_speed(CPP1,Motor1Data); 
 
  }

  Serial.println(Motor1Data.set_Move_Relative);
  
   if(Motor2Data.get_enable & Motor2Data.get_ready){
    move_relative(CPP2,Motor2Data); 
    //Motor2Data.set_Move_speed =Motor2Data.set_Move_Relative;
    //move_speed(CPP2,Motor2Data); 
  } 

}

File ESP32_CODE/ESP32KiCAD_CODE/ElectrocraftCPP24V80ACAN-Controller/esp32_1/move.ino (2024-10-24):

void move_relative(byte CPP, MotorData& Motor1Data){

  //Serial.println(Motor1Data.set_Move_Relative);
  
  struct can_frame canMsg; 

  // Example values for constructing the 29-bit identifier
  byte priority = 0x01;       // Priority = 1
  byte serviceBit = 0x01;     // Service Bit = 1 (always 1)
  byte requestBit = 0x01;     // Request Bit = 1 (Request = 1, Response = 0)
  byte serviceID = 0x41;      // GET service command = 0x00
  byte axisGroup = 0x01;      // Axis = 1 (for single drive)
  byte destID = CPP;         // Destination ID = 01
  byte hostBit = 0x00;        // Host Bit = 1 (for host PC)
  byte sourceID = 0x30;       // Source ID = 30

  // Construct the 29-bit CAN ID
  unsigned long canID = constructCANID(priority, serviceBit, requestBit, serviceID, axisGroup, destID, hostBit, sourceID);
 
  // Prepare the CAN message with a 29-bit identifier (Extended frame)
  canMsg.can_id = canID;     // 29-bit ID
  canMsg.can_id |= CAN_EFF_FLAG;  // Set the Extended Frame Format (EFF) flag
  canMsg.can_dlc = 0x05;        // 5 data bytes

  canMsg.data[0] = 0x03;
  canMsg.data[1] = Motor1Data.set_Move_Relative & 0xFF;
  canMsg.data[2] = (Motor1Data.set_Move_Relative >> 8) & 0xFF;
  canMsg.data[3] = (Motor1Data.set_Move_Relative >> 16) & 0xFF;
  canMsg.data[4] = (Motor1Data.set_Move_Relative >> 24) & 0xFF;

  // Send the message
  if (mcp2515.sendMessage(&canMsg) == MCP2515::ERROR_OK) {
    Serial.println(" sending move_relative command");
    Serial.println(canMsg.data[2], HEX);
  } else {
    Serial.println("Error sending move_relative command");
  }

    // Delay to allow the motor to reply
  delay(10);

   struct can_frame rcanMsg;
  // Check for received CAN messages (the response from the motor)
  if (mcp2515.readMessage(&rcanMsg) == MCP2515::ERROR_OK) {
     Serial.println(" Successsful move_relative command");
     Serial.println(rcanMsg.data[0], HEX);
     Serial.println(rcanMsg.data[1], HEX);
  } else {
    Serial.println("No CAN message received");
  }
}

void move_current(byte CPP){

  struct can_frame canMsg; 

  // Example values for constructing the 29-bit identifier
  byte priority = 0x01;       // Priority = 1
  byte serviceBit = 0x01;     // Service Bit = 1 (always 1)
  byte requestBit = 0x01;     // Request Bit = 1 (Request = 1, Response = 0)
  byte serviceID = 0x41;      // GET service command = 0x00
  byte axisGroup = 0x01;      // Axis = 1 (for single drive)
  byte destID = CPP;         // Destination ID = 01
  byte hostBit = 0x00;        // Host Bit = 1 (for host PC)
  byte sourceID = 0x30;       // Source ID = 30

  // Construct the 29-bit CAN ID
  unsigned long canID = constructCANID(priority, serviceBit, requestBit, serviceID, axisGroup, destID, hostBit, sourceID);
 
  // Prepare the CAN message with a 29-bit identifier (Extended frame)
  canMsg.can_id = canID;     // 29-bit ID
  canMsg.can_id |= CAN_EFF_FLAG;  // Set the Extended Frame Format (EFF) flag
  canMsg.can_dlc = 0x05;        // 3 data bytes

  canMsg.data[0] = 0x10;
  canMsg.data[1] = Motor1Data.set_Move_current & 0xFF;
  canMsg.data[2] = (Motor1Data.set_Move_current >> 8) & 0xFF;
  canMsg.data[3] = (Motor1Data.set_Move_current >> 16) & 0xFF;
  canMsg.data[4] = (Motor1Data.set_Move_current >> 24) & 0xFF;

  // Send the message
  if (mcp2515.sendMessage(&canMsg) == MCP2515::ERROR_OK) {
    //Serial.println(" sending move_current command");
  } else {
    Serial.println("Error sending move_current command");
  }

    // Delay to allow the motor to reply
  delay(10);

  struct can_frame rcanMsg;
  // Check for received CAN messages (the response from the motor)
  if (mcp2515.readMessage(&rcanMsg) == MCP2515::ERROR_OK) {
      Serial.println(" Successsful move_current command");
     Serial.println(rcanMsg.data[0], HEX);
  } else {
    Serial.println("No CAN message received");
  }
  
}

void move_speed(byte CPP, MotorData& MotorxData){

  struct can_frame canMsg; 

  // Example values for constructing the 29-bit identifier
  byte priority = 0x01;       // Priority = 1
  byte serviceBit = 0x01;     // Service Bit = 1 (always 1)
  byte requestBit = 0x01;     // Request Bit = 1 (Request = 1, Response = 0)
  byte serviceID = 0x41;      // 
  byte axisGroup = 0x01;      // Axis = 1 (for single drive)
  byte destID = CPP;         // Destination ID = 01
  byte hostBit = 0x00;        // Host Bit = 1 (for host PC)
  byte sourceID = 0x30;       // Source ID = 30

  // Construct the 29-bit CAN ID
  unsigned long canID = constructCANID(priority, serviceBit, requestBit, serviceID, axisGroup, destID, hostBit, sourceID);
 
  // Prepare the CAN message with a 29-bit identifier (Extended frame)
  canMsg.can_id = canID;     // 29-bit ID
  canMsg.can_id |= CAN_EFF_FLAG;  // Set the Extended Frame Format (EFF) flag
  canMsg.can_dlc = 0x05;        // 3 data bytes

  canMsg.data[0] = 0x20;
  canMsg.data[1] = MotorxData.set_Move_speed & 0xFF;
  canMsg.data[2] = (MotorxData.set_Move_speed >> 8) & 0xFF;
  canMsg.data[3] = (MotorxData.set_Move_speed >> 16) & 0xFF;
  canMsg.data[4] = (MotorxData.set_Move_speed >> 24) & 0xFF;

  // Send the message
  if (mcp2515.sendMessage(&canMsg) == MCP2515::ERROR_OK) {
    //Serial.println(" sending move_speed command");
  } else {
    Serial.println("Error sending move_speed command");
  }

    // Delay to allow the motor to reply
  delay(10);

  struct can_frame rcanMsg;
  // Check for received CAN messages (the response from the motor)
  if (mcp2515.readMessage(&rcanMsg) == MCP2515::ERROR_OK) {
    //Serial.println(" Successsful move_speed command");
    //Serial.println(rcanMsg.data[0], HEX);
  } else {
    Serial.println("No CAN message received");
  }
  
}

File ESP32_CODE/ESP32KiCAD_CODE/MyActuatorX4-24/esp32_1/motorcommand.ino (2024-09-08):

// Helper function to convert float to 4 bytes
void floatToBytes(float value, uint8_t* bytes) {
  union {
    float floatVal;
    uint8_t byteArray[4];
  } floatUnion;
  
  floatUnion.floatVal = value;
  for (int i = 0; i < 4; i++) {
    bytes[i] = floatUnion.byteArray[i];
  }
}

// Helper function to convert 4 bytes to float
float bytesToFloat(uint8_t* bytes) {
  union {
    float floatVal;
    uint8_t byteArray[4];
  } floatUnion;
  
  for (int i = 0; i < 4; i++) {
    floatUnion.byteArray[i] = bytes[i];
  }
  return floatUnion.floatVal;
}

// Function to send position control command
void sendPositionControlCommand(uint16_t canID, uint8_t mode, float position, uint16_t speed, uint16_t currentThreshold, uint8_t returnStatus) {

    struct can_frame canMsg;
    canMsg.can_id  = canID;  // CAN ID (e.g., 0x204 + motorID)
    canMsg.can_dlc = 8;      // Message length (8 bytes)

    // Clear the CAN message data
    memset(canMsg.data, 0, sizeof(canMsg.data));

    // Convert float position to 32-bit integer representation
    uint32_t positionInt = *(reinterpret_cast<uint32_t*>(&position));

    // Byte 0: Motor mode (3 bits) + 5 MSBs of position
    canMsg.data[0] = ((mode & 0x07) << 5) | ((positionInt >> 27) & 0x1F);

    // Byte 1: Next 8 bits of position
    canMsg.data[1] = (positionInt >> 19) & 0xFF;

    // Byte 2: Next 8 bits of position
    canMsg.data[2] = (positionInt >> 11) & 0xFF;

    // Byte 3: Next 8 bits of position
    canMsg.data[3] = (positionInt >> 3) & 0xFF;

    // Byte 4: Remaining 3 bits of position + 5 MSBs of speed
    canMsg.data[4] = ((positionInt & 0x07) << 5) | ((speed >> 10) & 0x1F);

    // Byte 5: Next 8 bits of speed
    canMsg.data[5] = (speed >> 2) & 0xFF;

    // Byte 6: Last 2 bits of speed + 6 MSBs of current threshold
    canMsg.data[6] = ((speed & 0x03) << 6) | ((currentThreshold >> 6) & 0x3F);

    // Byte 7: Remaining 6 bits of current threshold + 2 bits for return status
    canMsg.data[7] = ((currentThreshold & 0x3F) << 2) | (returnStatus & 0x03);

    
  // Send the CAN message
  if (mcp2515.sendMessage(&canMsg) == MCP2515::ERROR_OK) {
    //Serial.println("Position control command sent successfully");
  } else {
    Serial.println("Error: Failed to send position control command");
  }

  delay(20);  // Wait 10 milliseconds before checking for a response

  // Check for received CAN messages (the response from the motor)
  if (mcp2515.readMessage(&canMsg) == MCP2515::ERROR_OK) {
    //Serial.print("Received CAN message with ID: 0x");
    //Serial.println(canMsg.can_id, HEX);
    
    // Print received data
    //Serial.print("CAN ID Response Data: ");
    for (int i = 0; i < canMsg.can_dlc; i++) {
     // Serial.print(canMsg.data[i], HEX);
     // Serial.print(" ");
    }
   // Serial.println();

    // Decode the return status from Byte 7
    uint8_t responseReturnStatus = canMsg.data[7] & 0x03;
    //Serial.print("Return Status: ");
    //Serial.println(responseReturnStatus);

  } else {
    //Serial.println("No CAN message received");
  }
}


void MotorZeroSetting(uint16_t canID) {
  
  struct can_frame canMsg;
  
  canMsg.can_id  = 0x7FF;    
  canMsg.can_dlc = 4;            
  canMsg.data[0] = canID>>8;        
  canMsg.data[1] = canID;
  canMsg.data[2] = 0x00;
  canMsg.data[3] = 0x03;
  
  // Send CAN message
  if (mcp2515.sendMessage(&canMsg) == MCP2515::ERROR_OK) {
    Serial.print("Sent Zero Setting");
    Serial.print(canID, HEX);
    Serial.print(" to 0x");
  } else {
    Serial.println("Error sending CAN message to set CAN ID");
  }

  // Delay to ensure the command is processed
  delay(1000);

  // Check for received CAN messages (the response from the motor)
  if (mcp2515.readMessage(&canMsg) == MCP2515::ERROR_OK) {
    Serial.print("Received CAN message with ID: 0x");
    Serial.println(canMsg.can_id, HEX);
    
    // Print received data (assuming it includes CAN ID info)
    Serial.print("CAN ID Response Data: ");
    for (int i = 0; i < canMsg.can_dlc; i++) {
      Serial.print(canMsg.data[i], HEX);
      Serial.print(" ");
    }
    Serial.println();

    // Check if the response data includes a CAN ID
    // Typically, the CAN ID will be part of the response. You might need to parse it accordingly.
    uint8_t receivedID = canMsg.data[0]; // For example, CAN ID might be stored in the first byte
    
  } else {
    Serial.println("No CAN message received");
  }

   delay(1000);
}

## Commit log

2024-05-02 Added pcb files
    [ESB32CARRIER.brd, ESB32CARRIER.sch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]
2024-08-21 Changed pcb to KiCAD
    [ESB32CARRIER.brd, ESB32CARRIER.sch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]
2024-08-21 updated PCB
    [ESP32WROOM30PIN_CARRIER_BOARD_KELLA-B_Cu.gbr, ESP32WROOM30PIN_CARRIER_BOARD_KELLA-B_Mask.gbr, ESP32WROOM30PIN_CARRIER_BOARD_KELLA-B_Paste.gbr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]
2024-08-21 Picture esp32 added
2024-08-22 Added soldered
2024-08-22 Added printed PCB
2024-09-04 Esp32code updated
